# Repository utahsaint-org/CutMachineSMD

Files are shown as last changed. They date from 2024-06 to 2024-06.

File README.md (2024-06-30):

# CutMachineSMD

The Resistor and LED Cutting machine is a community project to make mass-production of small SMD components cut to specific unit sizes faster and easier to make for our highly popular MiniBadge initiatives and standards.  This machine has been used in mass-production and works great for feeding and cutting several component types.

#### Key Features
- SMD Tape Cutting
- Custom Menu-Driven Calibration Settings
- Test Cutting and Program Cutting
- Sharpie Attachment to allow color-coding of components as they are cut
- Community Contribution

# Parts List:  

For convenience I have an Amazon List for most parts: https://a.co/ecXTVj9

- 2020 Extruded Aluminium cut to
  - 2x 30cm - Top/Bottom
  - 3x 26cm - Verticals
  - 2x 20cm - Legs
  - 1x 155mm - Horizontal Crossmember
  - 1x 155mm - Roll Attachment Crossmember (Optional)
- 2020 Series Connectors and Corner Bracket Set (30 Piece)
- Bracket L-Type Internal Connectors for 2020 Series
- 4x 2020 Series Rubber Feet
- Stepper Motors
  - NEMA23 4.2Amp Motor (StepperOnline 23HS45-4204S)
  - NEMA17 1.2Amp Motor (StepperOnline 17HS19-2004S)
- Motor Drivers
  - 1x EASON Stepper Motor Driver TB6600 4A
  - 2x Stepper Motor Driver DRV8825
- Cutting Blades - 9mm Knife Replacement Blade Cartridge
- Electronics
  - Arduino Uno R3 or similar device.
  - HiLetgo CNC Drive Expansion Board (CNC Shield)
  - 2.42" 128x64 OLED LCD Display (SSD1309) i2C
- M3 Hardware
  - Assorted M2 Length Screws, Nuts, Washers
  - Assorted M3 Length Screws, Nuts, Washers
  - Assorted M5 Length Screws, Nuts, Washers
  - M3 Lever Steering Linkage
  - M3 Link Strut shaft 35mm
- 1x Miniature Linear Sliding Guideway Rail 150mm
- Power Supplies
  - 12VDC 15A Linear Power Supply
  - 12VDC to 5VDC Stepdown Regulator to power the Arduino (Optional)
- Components for PCBs ([Digikey](https://digikey.com)/[Mouser](https://mouser.com) or Similar)
  - 4x 6mm THT PushButton Switchs
  - 6x 10KΩ SMD  1206 Resistors
  - 1x 220Ω SMD  1206 Resistor
  - 1x 2.2KΩ SMD 1206 Resistor
  - 7+ Position Right-Angle PIN Headers
  - 3+ Position Straight PIN Headers
- PCBs Ordered (JLC_PCB or Similar)
  - [1x Button_Board](https://github.com/utahsaint-org/CutMachineSMD/tree/main/CuttingMachine_PCB/Buttons/Gerbers) 
  - [2x Sensor_Board](https://github.com/utahsaint-org/CutMachineSMD/tree/main/CuttingMachine_PCB/Sensor/Gerbers)
    
# Setup and Configuration

### OLED Screen Modification
The OLED screen typically comes configured for SPI interface, and we are using I2C protocol in this project.   As such, you will need to modify the OLED screen by bridging several solder pads to put the screen into I2C configuration.   You will need to disconnect the ribbon-cable and underneath you will need to bridge the solder pads labeled: R9, R10, R11, R12.  You will also need to remove the Resistor labeled R8. (Follow the published instructions for the screen to make this modification)

### Building the Framework
The Framework for the machine is fairly stratight-forward.  The 30cm struts are mounted as the top and bottom rails.  Use normal corner attachments to make the connections.  The 26cm vertical struts are attached with one in the middle and the other two are attached on the edges to make a 30cm x 30cm frame.  The center vertical is attached at 105mm spacing from center to center or 85mm Internal spacing.  You can use the Acrylic Cut Head mount as the spacing guide.   Lastly the cross-member can be attached at the approximate horizontal mid-point (125mm internal spacing).  20cm Legs are mounted horizontally outside the frame for stability.  The frame with mounted motors becomes back-heavy so I personally offset the legs to favor the back side for better support.

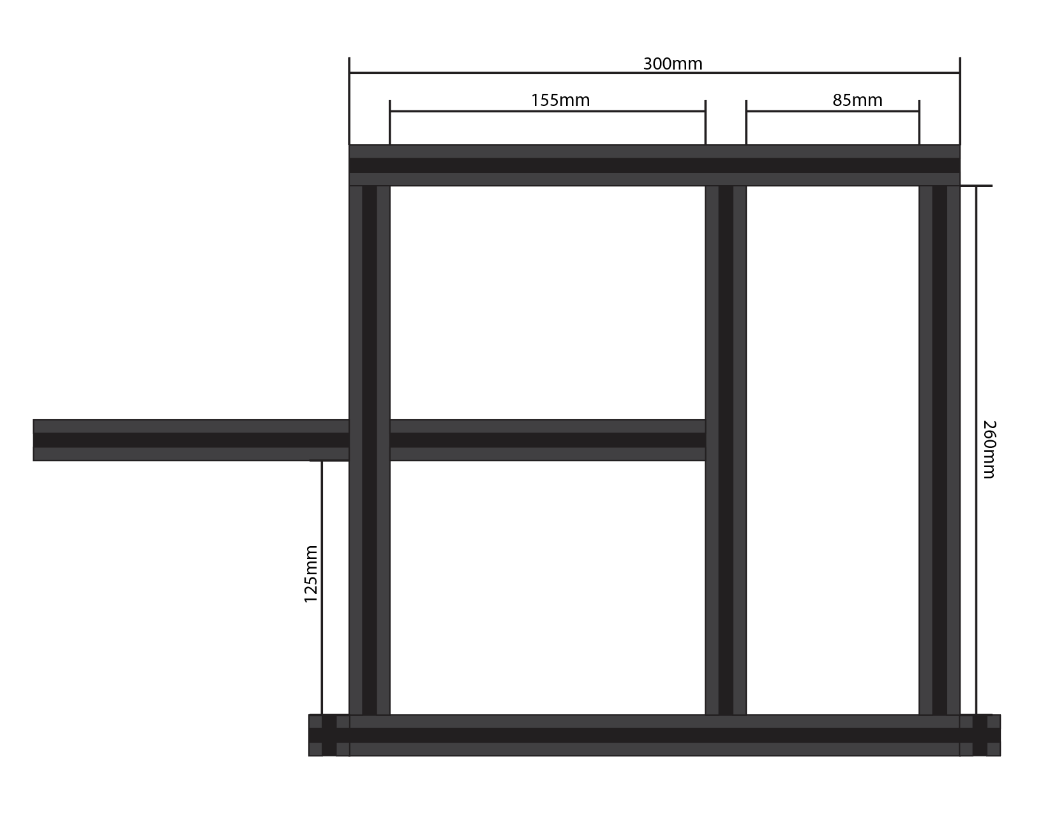
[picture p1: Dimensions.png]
Frame Dimensions


### Power Supply
Picking the right power-supply is an important aspect of any Stepper Motor configuration.   For this machine I used a 12v 15A capable power supply.   This provided all of the power I needed to run both motors and the arduino electronics.

### 3D Printing
Several of the STL designs need **supports** to be printed to ensure they are printed correctly.
NOTE: There are two Cut Heads.  One for Resistors and one for LEDs.

### Assembly
Here is what you are building:
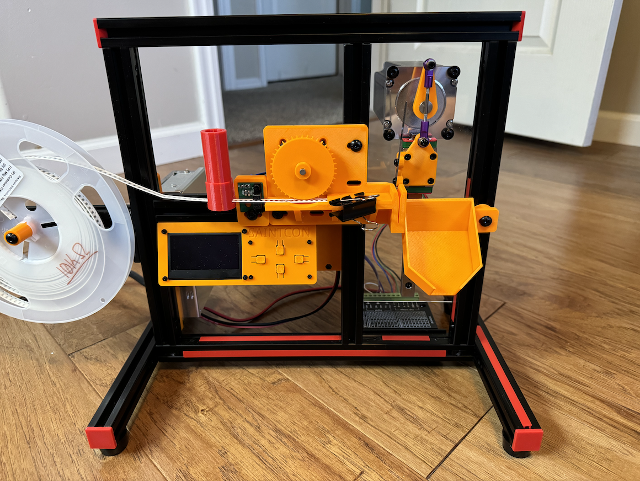
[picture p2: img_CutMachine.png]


- Build the Framework as described above.
- Attach the AcrylicCutHead on the Back Side of the machine
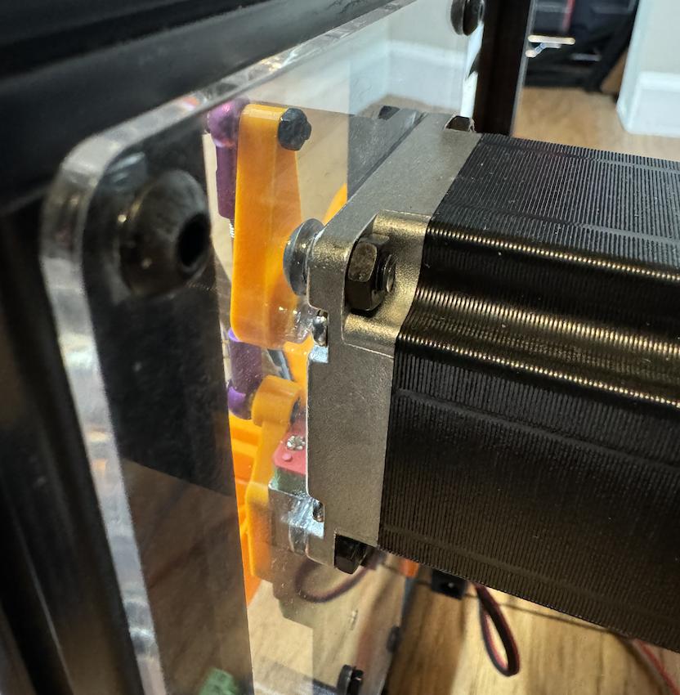
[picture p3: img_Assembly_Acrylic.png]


- Attach a RazorBlade to the Printed CutHead on the outside
  - Bottom Screw goes THRU the hole on the blade
  - Top Screw squeezes the blade to the head using a washer
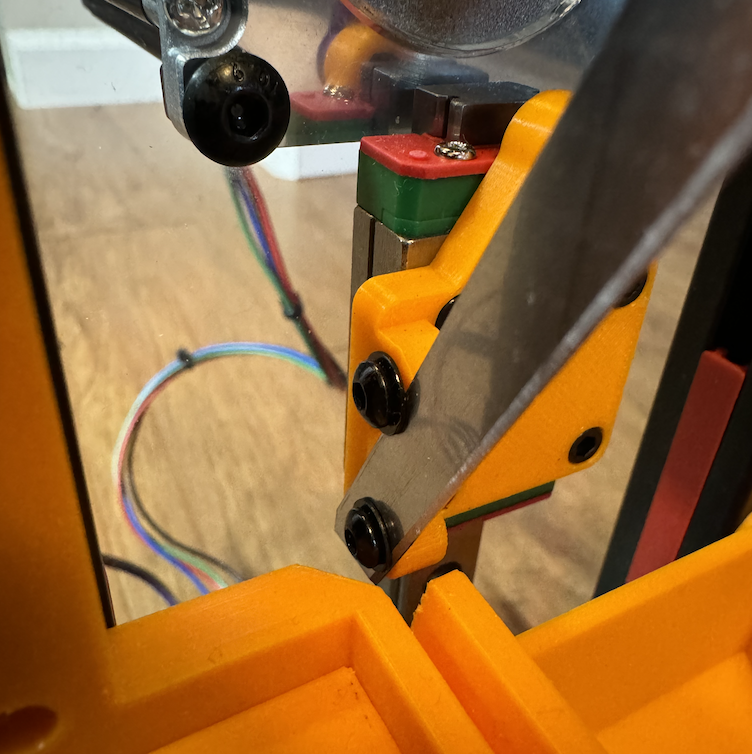
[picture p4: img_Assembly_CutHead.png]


- Attach the Razor CutHead to the Slider Rail
- Attach the FeedHead to the center rails (Horizontal and Vertical)
  - Align the razor to the slit of the Feedhead
- Attach and Connect the Display (See connections diagram)

### Firmware and Flashing
The Firmware is available in the repo.  Use the Arduino IDE application to program the Arduino board.  There are several sources of documentation or videos that can instruct you on how to install and use this program.  If you have issues, limited technical support is available on the <a href=https://discord.gg/saintcon>SAINTCON Discord Server</a> #minibadge-creators

You will need to install the following libraries:
- Adafruit GFX
- Adafruit SSD1306 Display

**Board Type should be Arduino Uno (R3)**

Open the *CuttingMachine_Firmware.ino* in the Arduino IDE program
Compile and upload the Firmware using the appropriate COM Port

### Connections
Connections for all of the components are outlined in the diagram below.

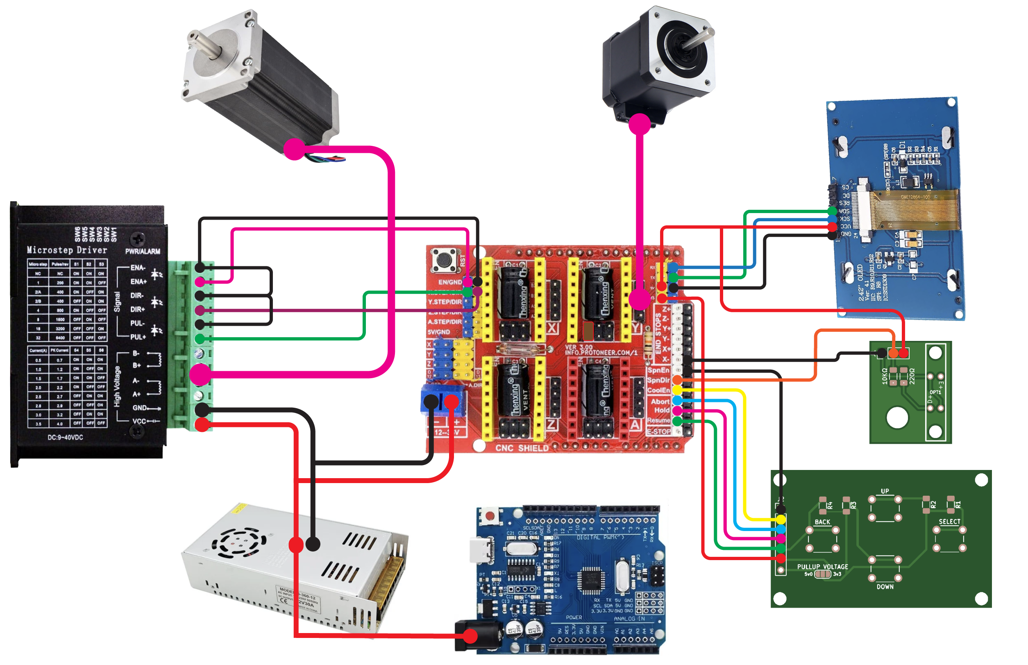
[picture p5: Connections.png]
Electrical Connections


### PCB Boards
The PCB Boards Gerbers are included in this repo.  The following instructions will help you assemble the boards and connect them properly.

#### Button_Board
- R1, R2, R3, R4 are all **10k Ohm** resistors.
- Buttons are THT 6mm Momentary Switch.
- Right-angle PIN HEADERS are suggested exiting out the back.
- Use a Solder Jumper to connect either 5v or 3v3. (Recommended you use 3v3)
- Attach the Board with M2 Screws/Bolts to the Display Controller.
- Attach the Connectors to CNC Shield as labeled in the Connections Diagram.

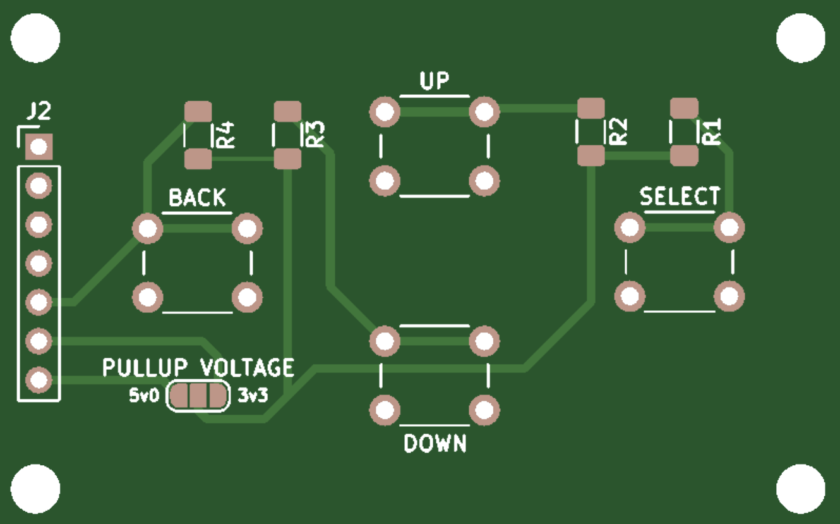
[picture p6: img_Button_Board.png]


#### Sensor_Board
- R1 is 10K Ohm
- R2 is 470 Ohm (if using it as presence sensor)
- R2 is 2.2K Ohm (If used as tape position sensor)
- PIN HEADERS are 3 Position
- Attach the Board with the M5 Screw to the FeedHead
  
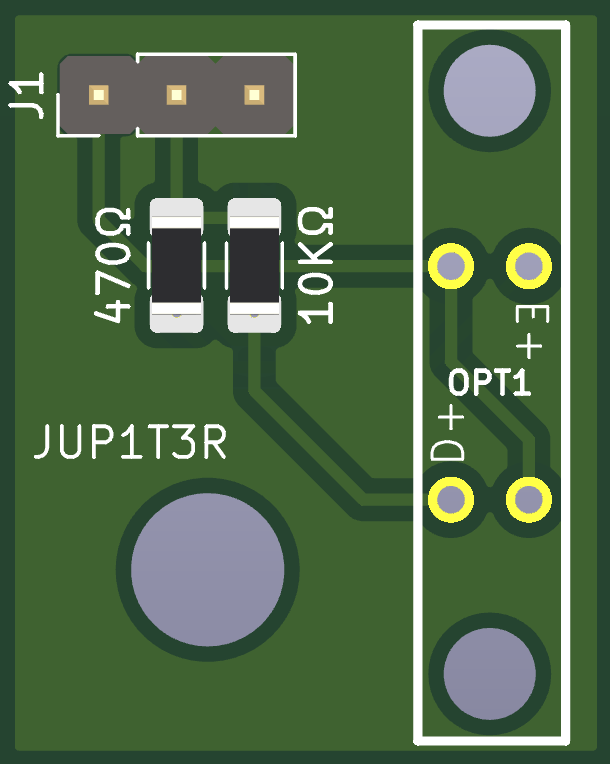
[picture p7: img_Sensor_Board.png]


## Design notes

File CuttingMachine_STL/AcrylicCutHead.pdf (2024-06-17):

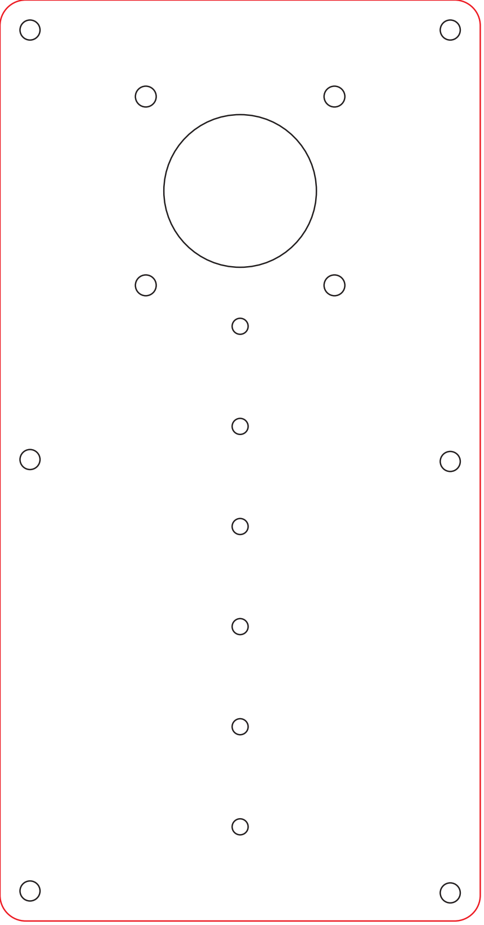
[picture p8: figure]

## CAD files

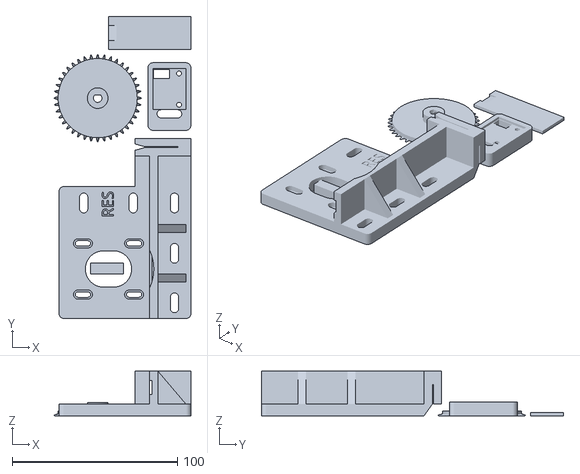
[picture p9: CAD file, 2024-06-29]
CuttingMachine_STL/RES-Cut-Head-MK11.stl
83.0 x 183.0 x 27.0

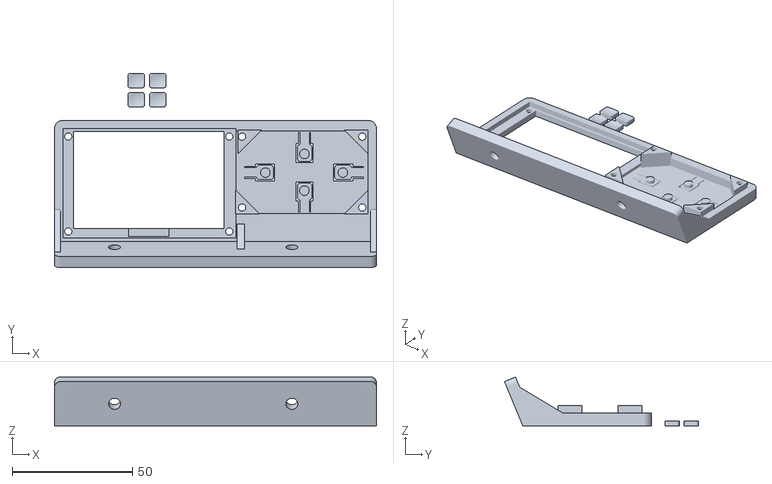
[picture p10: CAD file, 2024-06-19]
CuttingMachine_STL/Display-Face-Buttons-MK10.stl
134.0 x 80.8 x 20.4

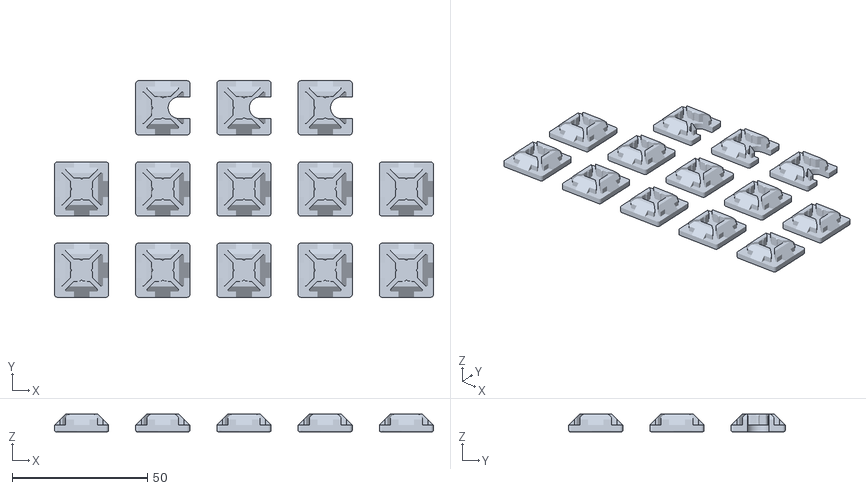
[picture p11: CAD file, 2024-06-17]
CuttingMachine_STL/EndCaps-2024-MK10.stl
140.0 x 80.0 x 6.50

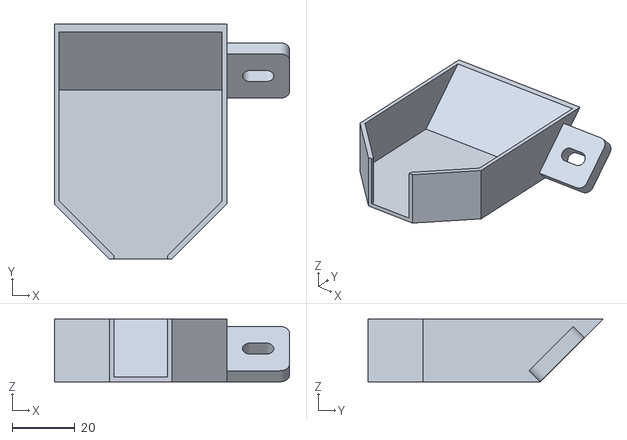
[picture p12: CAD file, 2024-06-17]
CuttingMachine_STL/Collection-Tray-2024-MK10.stl
75.0 x 75.0 x 20.0

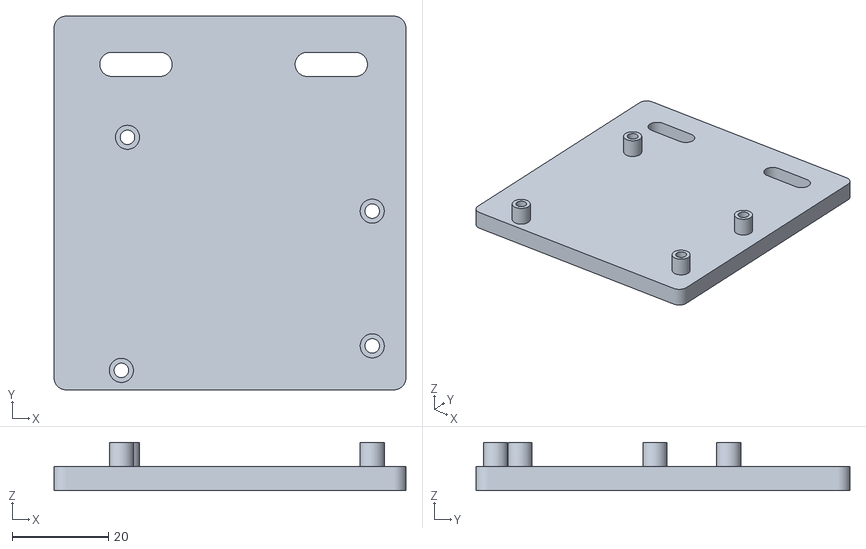
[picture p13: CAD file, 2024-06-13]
CuttingMachine_STL/Arduino-Holder-2024-MK10.stl
73.0 x 77.5 x 10.0

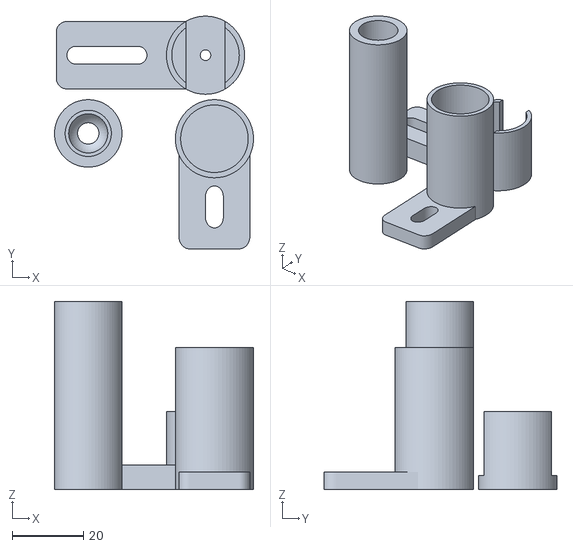
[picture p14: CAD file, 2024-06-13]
CuttingMachine_STL/Sharpie-Holder-MK11.stl
56.0 x 65.5 x 53.0

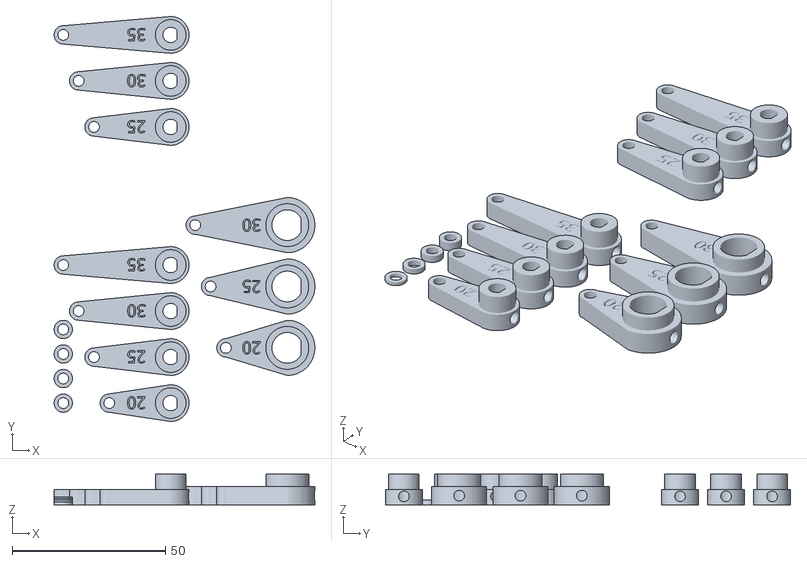
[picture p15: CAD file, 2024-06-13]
CuttingMachine_STL/Cutting-Arm-2024-MK10.stl
85.0 x 132.0 x 10.0

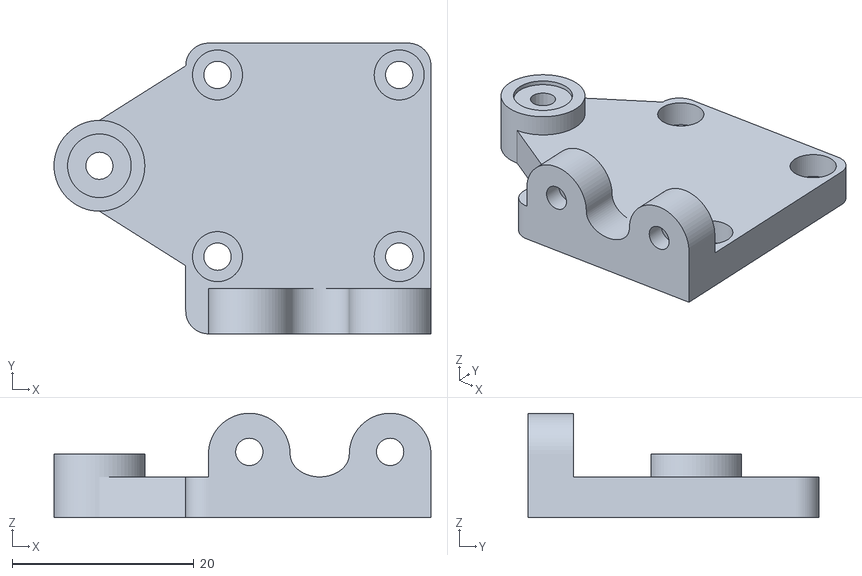
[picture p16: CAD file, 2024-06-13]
CuttingMachine_STL/Cutting-Head-2024-MK10.stl
41.5 x 32.0 x 11.5

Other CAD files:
CuttingMachine_STL/LED-Cut-Head-MK11.stl

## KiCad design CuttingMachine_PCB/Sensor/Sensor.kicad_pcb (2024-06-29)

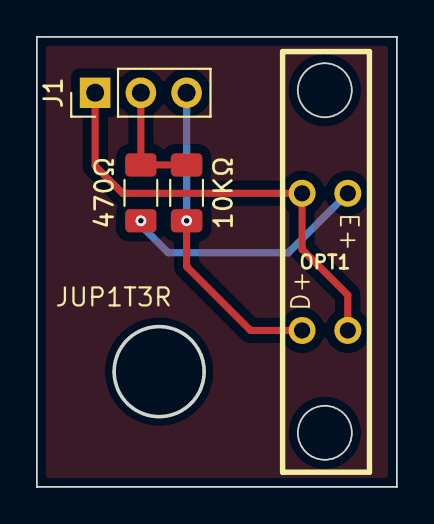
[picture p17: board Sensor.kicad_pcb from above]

Board: 2 copper layers, 20.0 x 25.0 mm, 4 parts (0 on the bottom side), 4 nets.

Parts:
10KΩ: 220; R_1206_3216Metric_Pad1.30x1.75mm_HandSolder
470Ω: 10k; R_1206_3216Metric_Pad1.30x1.75mm_HandSolder
J1: Conn_01x03_Pin; PinHeader_1x03_P2.54mm_Vertical
OPT1: MOC7811

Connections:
unnamed: J1.1, OPT1.2 (E-), OPT1.4 (D-)
unnamed: 10KΩ.1, 470Ω.1, J1.2
unnamed: 10KΩ.2, J1.3, OPT1.3 (D+)
unnamed: 470Ω.2, OPT1.1 (E+)

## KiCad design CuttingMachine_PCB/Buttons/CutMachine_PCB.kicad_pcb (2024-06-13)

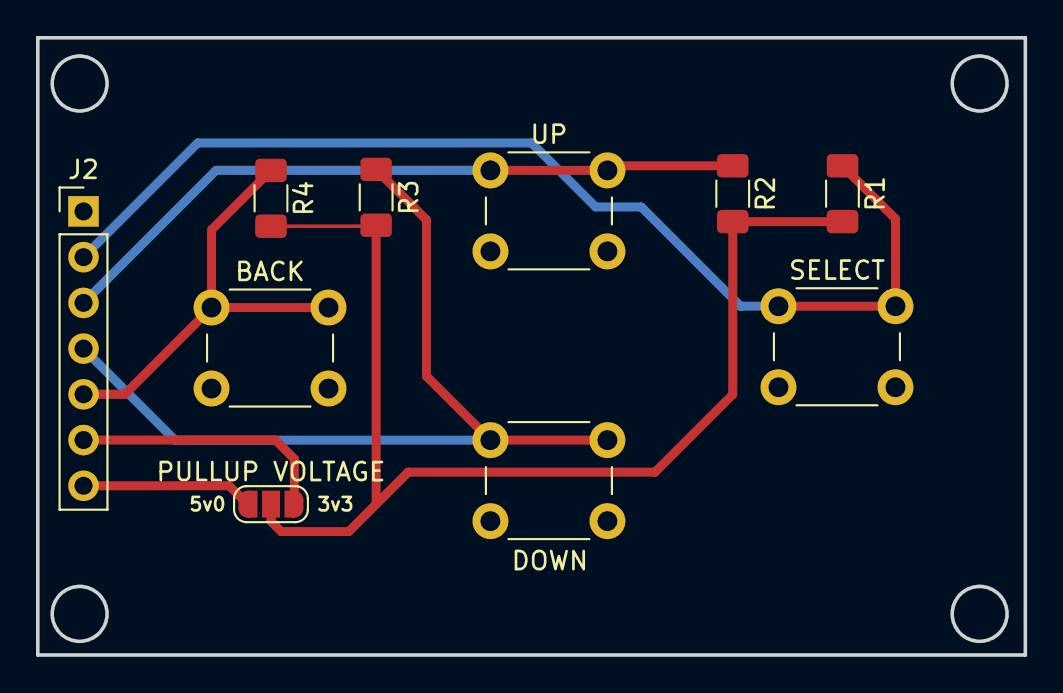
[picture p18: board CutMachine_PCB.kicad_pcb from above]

Board: 2 copper layers, 54.9 x 34.3 mm, 10 parts (0 on the bottom side), 8 nets.

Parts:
BACK: BACK; SW_PUSH_6mm_H4.3mm
J2: Conn_01x07_Pin; PinHeader_1x07_P2.54mm_Vertical
PULLUP VOLTAGE: SolderJumper_3_Open; SolderJumper-3_P1.3mm_Open_RoundedPad1.0x1.5mm_NumberLabels
R1, R2, R3, R4: PULLUP; R_1206_3216Metric_Pad1.30x1.75mm_HandSolder
SELECT: SELECT; SW_PUSH_6mm_H4.3mm
SW3: DOWN; SW_PUSH_6mm_H4.3mm
UP: UP; SW_PUSH_6mm_H4.3mm

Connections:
+3.3V: J2.6, PULLUP VOLTAGE.3 (B)
+5V: J2.7, PULLUP VOLTAGE.1 (A)
GND: BACK.2, J2.1, SELECT.2, SW3.2, UP.2
unnamed: J2.2, R1.1, SELECT.1
unnamed: J2.3, R2.1, UP.1
unnamed: J2.4, R3.1, SW3.1
unnamed: BACK.1, J2.5, R4.1
unnamed: PULLUP VOLTAGE.2 (C), R1.2, R2.2, R3.2, R4.2

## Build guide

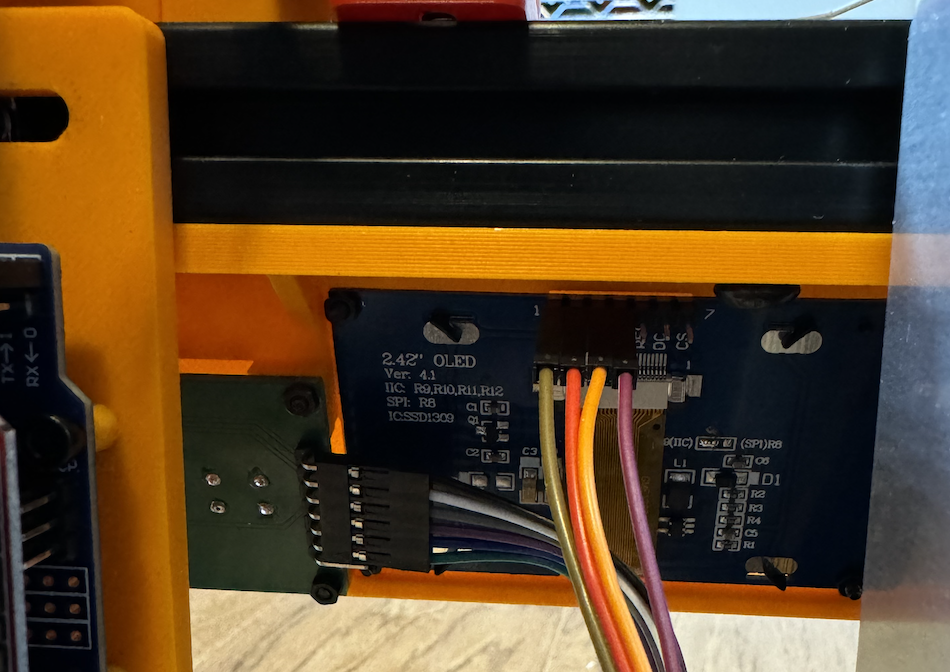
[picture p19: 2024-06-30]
img_Assembly_Display.png

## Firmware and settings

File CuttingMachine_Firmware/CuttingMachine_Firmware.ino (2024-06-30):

#include <Wire.h>

#include <Adafruit_GFX.h> // Library for GFX
#include <Adafruit_SSD1306.h> // Library for the OLED Screen
#include <avr/wdt.h> // Library for Watchdog
#include <avr/sleep.h> // Library to Sleep

#include "Assets.h" // Library of Images and Bitmaps
#include "Actions.h" // Library of most machine actions

#define version "1.0.5" // Several Updates
#define cuttype "RES" // RES or LED set for Different Types

#define SCREEN_WIDTH 128
#define SCREEN_HEIGHT 64
#define OLED_RESET - 1
Adafruit_SSD1306 display(SCREEN_WIDTH, SCREEN_HEIGHT, & Wire, OLED_RESET);

// Define buttons
#define BUTTON_UP A0
#define BUTTON_DOWN A1
#define BUTTON_BACK A2
#define BUTTON_SELECT A3
// Define Sensors
#define SENSOR_TAPE 13
#define SENSOR_UNIT 12

#define CUT_STEP 2 // Cutter Motor Stepper Pin
#define CUT_DIR 5 // Cutter Motor Direction Pin
#define FEED_STEP 3 // Feeder Motor Stepper Pin
#define FEED_DIR 6 // Feeder Motor Direction Pin
#define ENABLE 8 // Motor Enable Pin

int menuIndex = 0;
int submenuIndex = 0;
bool inSubMenu = false;
unsigned long lastActivityTime = 0;
const unsigned long inactivityTimeout = 600000;  // 10 Minutes in milliseconds

// Default Variable Settings
int setSize = 1; // Size of the units |*|*|*|*|*|
int setUnits = 1; // How many pieces get cut by default
int setInterval = 4; // Tape Interval in millimeters

// Debounce settings
const unsigned long debounceDelay = 300; // milliseconds
unsigned long lastDebounceTime = 10;

void setup() {
  // Setup Buttons used for Navigation (Up, Down, Back, Select)
  pinMode(BUTTON_UP, INPUT_PULLUP);
  pinMode(BUTTON_DOWN, INPUT_PULLUP);
  pinMode(BUTTON_BACK, INPUT_PULLUP);
  pinMode(BUTTON_SELECT, INPUT_PULLUP);
  // Setup PIN for Tape Presence Sensor
  pinMode(SENSOR_TAPE, INPUT);
  // Setup PINs for Motor Controls for Feed and Cut
  pinMode(CUT_STEP, OUTPUT);
  pinMode(CUT_DIR, OUTPUT);
  pinMode(FEED_STEP, OUTPUT);
  pinMode(FEED_DIR, OUTPUT);
  // Setup PIN for enableing Motors
  pinMode(ENABLE, OUTPUT);
  // Disable Motors until we enter Main Menu HIGH == DISABLED
  digitalWrite(ENABLE, HIGH);

  // Initialize the OLED display
  display.begin(SSD1306_SWITCHCAPVCC, 0x3C);
  display.clearDisplay();
  // Display Firmware and Logo
  FirmwareDisplay();      //Display Firmware Version
  LogoDisplay();          //Display Logo Bootscreen
}

  // Define Frame Control Variable for graphics
  int frame=0;

void loop() {
  // Watch for SELECT Button to enter the Menu
  if (readButton(BUTTON_SELECT) == true) {
    lastActivityTime = millis();
    navigateMenu();
  }
  // Disable Motors if the UP Button was pressed in Idle Screen
  if (readButton(BUTTON_UP) == true) { 
    digitalWrite(ENABLE, HIGH); 
    lastActivityTime = millis();
  }
  // Watch for inactivity and enter sleep mode
  if (millis() - lastActivityTime > inactivityTimeout) {
    enterSleepMode();
  }
  // Display the Idle Screen Details
  display.clearDisplay();
  display.drawBitmap(78, 0, frames[frame], FRAME_WIDTH, FRAME_HEIGHT, 1);
  display.setCursor(0, 0);
  display.setTextSize(2);
  display.println(F("IDLE"));
  display.setTextSize(1);
  display.print(F("Size: "));
  display.println(setSize);
  display.print(F("Units: "));
  display.println(setUnits);
  // Show the state of the Tape Sensor
  if (digitalRead(SENSOR_TAPE) == LOW) {
    display.println(F("Sensor: LOW"));
  } else {
    display.println(F("Sensor: HIGH"));
  }
  // Show the state of Unit Sensor
  if (digitalRead(SENSOR_UNIT) == LOW) {
    display.println(F("Sensor: LOW"));
  } else {
    display.println(F("Sensor: HIGH"));
  }
  // Show the state of the Motors
  if (digitalRead(ENABLE) == LOW) {
    display.println(F("Motors: ENABLED"));
  } else {
    display.println(F("Motors: DISABLED"));
  }
  display.println(F("Press SELECT to Start"));
  display.display();
  frame = (frame + 1) % FRAME_COUNT;
  delay(FRAME_DELAY);
}


// Process to handle Button Press Bounces (Smooth UI Handling)
bool readButton(int buttonPin) {
  if (digitalRead(buttonPin) == LOW) {
    // Do no detect the press unless its longer than debounceDelay value
    if (millis() - lastDebounceTime > debounceDelay) {
      lastDebounceTime = millis();
      return true;
    }
  }
  return false;
}

// Firmware Screen display
void FirmwareDisplay() { display.clearDisplay(); display.setTextColor(WHITE); display.setTextSize(1); display.print(F("Firmware: ")); display.println(F(version)); display.display(); delay(1000); }
// Logo Boot display
void LogoDisplay() { display.clearDisplay(); display.drawBitmap(0, 0, SCLOGO, 128, 64, SSD1306_WHITE); display.display(); delay(1500);}

// Main Menu Navigation Routine
void navigateMenu() {
  // Enable Motors if the Menu is entered (sticky)
  digitalWrite(ENABLE, LOW);
  while (true) {
    displayMenu();
    if (readButton(BUTTON_SELECT) == true) {
      if (inSubMenu) {
        executeSubmenuOption();
      } else {
        enterSubMenu();
      }
    } else if (readButton(BUTTON_BACK) == true) {
      if (inSubMenu) {
        inSubMenu = false;
        submenuIndex = 0;
      } else {
        //displayIdleScreen();
        return;
      }
    } else if (readButton(BUTTON_UP) == true) {
      if (inSubMenu) {
        submenuIndex = (submenuIndex > 0) ? submenuIndex - 1 : getMaxSubMenuIndex();
      } else {
        menuIndex = (menuIndex > 0) ? menuIndex - 1 : 4; // Adjust this for Menu Number
      }
    } else if (readButton(BUTTON_DOWN) == true) {
      if (inSubMenu) {
        submenuIndex = (submenuIndex < getMaxSubMenuIndex()) ? submenuIndex + 1 : 0;
      } else {
        menuIndex = (menuIndex < 4) ? menuIndex + 1 : 0; // Adjust this for Menu Number
      }
    }
  }
}

void displayMenu() {
  display.clearDisplay();
  display.setTextColor(SSD1306_WHITE);
  display.setTextSize(1);
  display.setCursor(0, 0);
  if (!inSubMenu) {
    display.setTextSize(2);
    display.println(F("MAIN MENU"));
    display.setTextSize(1);
    if (menuIndex == 0) display.println(F("> CUT!"));
    else display.println(F("  Cut!"));
    if (menuIndex == 1) display.println(F("> SETTINGS"));
    else display.println(F("  Settings"));
    if (menuIndex == 2) display.println(F("> CALIBRATE"));
    else display.println(F("  Calibrate"));
    if (menuIndex == 3) display.println(F("> LOAD TAPE"));
    else display.println(F("  Load Tape"));
    if (menuIndex == 4) display.println(F("> RESET"));
    else display.println(F("  Reset"));
  } else {
    if (menuIndex == 0) {
      display.setTextSize(2);
      display.println(F("START CUT!"));
      display.setTextSize(1);
      if (submenuIndex == 0) {
        display.setTextSize(3);
        display.println(F("> GO!"));
      } else {
        display.setTextSize(3);
        display.println(F("  Go"));
      }
      if (submenuIndex == 1) {
        display.setTextSize(1);
        display.println(F("> TEST CUT"));
      } else {
        display.setTextSize(1);
        display.println(F("  Test Cut"));
      }
    }
    if (menuIndex == 1) {
      display.setTextSize(2);
      display.println(F("SETTINGS"));
      display.setTextSize(1);
      if (submenuIndex == 0) { 
        display.print(F("> Set Size: "));
        display.println(setSize);
      } else { 
        display.print(F("  Set Size: "));
        display.println(setSize);
      }
      if (submenuIndex == 1) {
        display.print(F("> Set Units: "));
        display.println(setUnits);
      } else {
        display.print(F("  Set Units: "));
        display.println(setUnits);
      }
    }
    if (menuIndex == 2) {
      display.setTextSize(2);
      display.println(F("CALIBRATE"));
      display.setTextSize(1);
      if (submenuIndex == 0) display.println(F("> ADJUST FWD"));
      else display.println(F("  Adjust Fwd"));
      if (submenuIndex == 1) display.println(F("> ADJUST REV"));
      else display.println(F("  Adjust Rev"));
    }
    if (menuIndex ==3) {
      display.setTextSize(2);
      display.println(F("LOAD TAPE"));
      display.setTextSize(1);
      if (submenuIndex == 0) display.println(F("> LOAD TAPE"));
      else display.println(F("  Load Tape"));
      if (submenuIndex == 1) display.println(F("> UNLOAD TAPE"));
      else display.println(F("  Unload Tape"));
    }
      if (menuIndex ==4) {
      display.setTextSize(2);
      display.println("RESET?");
      display.setTextSize(1);
      if (submenuIndex == 0) display.println("> NO");
      else display.println("  No");
      if (submenuIndex == 1) display.println("> YES");
      else display.println("  Yes");
    }
  }
  display.display();
}

void enterSubMenu() {
  inSubMenu = true;
  submenuIndex = 0;
}

int getMaxSubMenuIndex() {
  switch (menuIndex) {
  case 0:
    return 1; // CUT! menu has 2 options: Go and Test Cut
  case 1:
    return 1; // Settings menu has 2 options: Set Size and Set Units
  case 2:
    return 1; // Calibrate menu has 2 options: Adjust FWD and Adjust REV
  case 3:
    return 1; // LoadTape Menu has 2 options
  case 4:
    return 1; // Reset menu has 2 options
  default:
    return 0;
  }
}

void executeSubmenuOption() {
  switch (menuIndex) {
  case 0: // CUT!
    if (submenuIndex == 0) runCutProgram();
    else if (submenuIndex == 1) runCutTest();
    break;
  case 1: // Settings
    if (submenuIndex == 0) changeSize();
    else if (submenuIndex == 1) changeUnits();
    break;
  case 2: // Calibrate
    if (submenuIndex == 0) runAdjustFWD();
    else if (submenuIndex == 1) runAdjustREV();
    break;
  case 3: // LoadTape Menu
    if (submenuIndex == 0) loadTape();
    else if (submenuIndex == 1) unloadTape();
    break;
  case 4: // Reset Menu
    if (submenuIndex == 0) resetNo();
    else if (submenuIndex == 1) resetYes();
    break;
  }
}

/// Sleep Mode Process
void enterSleepMode() {
  digitalWrite(ENABLE, HIGH);  // Disable Motors so they last longer
  lastActivityTime = millis();
  inSubMenu=false;
}

void resetNo()  { inSubMenu = false; }
void resetYes() {
  display.clearDisplay(); display.setCursor(0, 0); display.setTextSize(2); display.println(F("RESETTING!")); display.display();
  delay(2000);
  // Reboot Device
  wdt_enable(WDTO_15MS);
  while(1);
}

// Main Cutting Program
void runCutProgram() {
  display.clearDisplay();
  // Main process for Cutting
  for (int rp = 0; rp < setUnits; rp++) {
    // Display Cut Status (Units Cut)
    display.setCursor(0, 0); display.setTextSize(2); display.println("CUTTING"); display.setTextSize(3); display.setCursor(0, 24); display.print(" = "); display.println(rp + 1); display.display();
    // Sensor Check for Tape Existence (Stop and Display Error)
    if (digitalRead(SENSOR_TAPE) == LOW) {
      // Display Error Message
      display.clearDisplay(); display.setCursor(4, 7); display.setTextSize(2); display.println("!STOPPING!"); display.setTextSize(1); display.println("\n    Load or Check\n   component tape."); display.display();
      delay(500);
      // Blink the Display
      for (int i = 0; i < 20; i++) {
        if (i % 2 == 0) {
          display.invertDisplay(true);
        } else {
          display.invertDisplay(false);
        }
        display.display();
        delay(500);
      }
      // Stop and Return if the Sensor is tripped
      return;
    }
    FEED(setSize);  // Feed the Tape based on the Size Selected
    CUT();  // Cut the tape after the feed is complete
    lastActivityTime = millis();  // Keep from entering sleepMode while cutting
  }
  // Clear the cut head
  ClearFeeder(); // Clears the Feed Head
  delay(200);
  inSubMenu = false;
}

// This will cut one component and make one unit
// This is just for testing
void runCutTest() {
  FEED(1);
  CUT();
  ClearFeeder();
  delay(500);
  inSubMenu = false;
}

void ClearFeeder() {
  int ClearCount = 10;
  digitalWrite(FEED_DIR, LOW); // Set Forward
  for (int y = 0; y < ClearCount; y++) {
    digitalWrite(FEED_STEP, HIGH);
    delayMicroseconds(1700); // Fast Rotation
    digitalWrite(FEED_STEP, LOW);
    delayMicroseconds(1700); // Fast Rotation
  }
  digitalWrite(FEED_DIR, HIGH); // Set Reverse
  for (int y = 0; y < ClearCount; y++) {
    digitalWrite(FEED_STEP, HIGH);
    delayMicroseconds(1700); // Fast Rotation
    digitalWrite(FEED_STEP, LOW);
    delayMicroseconds(1700); // Fast Rotation
  }
  digitalWrite(FEED_DIR, LOW);
}

// Main CUT Process (One Full Rotation)
void CUT() {
  int cutsteps = 800;
  for (int x = 0; x < cutsteps; x++) {
    digitalWrite(CUT_STEP, HIGH);
    delayMicroseconds(90); // Fast Rotation
    digitalWrite(CUT_STEP, LOW);
    delayMicroseconds(90); // Fast Rotation
    display.clearDisplay();
  }
  delay(100);
}

// Main FEED Process
void FEED(int feedcount) {
  int feedsteps = feedcount * 10;
  digitalWrite(FEED_DIR, LOW); // Set Feed Forward for Feed
  for (int y = 0; y < feedsteps; y++) {
    digitalWrite(FEED_STEP, HIGH);
    delayMicroseconds(700); // Fast Rotation
    digitalWrite(FEED_STEP, LOW);
    delayMicroseconds(700); // Fast Rotation
  }
  delay(100);
}

// Future Tape Loading
void loadTape() {
  display.clearDisplay();
  display.setCursor(0, 0);
  display.println(F("LOAD Function not\nimplemented"));
  display.display();
  delay(2000);
}
// Future Tape Unloading
void unloadTape() {
  display.clearDisplay();
  display.setCursor(0, 0);
  display.println(F("UNLOAD Function not\nimplemented"));
  display.display();
  delay(2000);
}

void changeSize() {
  while (true) {
    if (readButton(BUTTON_UP) == true && setSize < 1000) setSize++;
    else if (readButton(BUTTON_DOWN) == true && setSize > 1) setSize--;
    //delay(150);
    if (readButton(BUTTON_SELECT) == true) break;
    display.clearDisplay();
    display.setCursor(0, 0);
    display.setTextSize(2);
    display.print("SET SIZE\n");
    display.setCursor(4, 17);
    display.setTextSize(3);
    display.println(setSize);
    // Display the size of the unit
    if (setSize >= 1) { display.drawBitmap(0, 51, RES, 7, 14, SSD1306_WHITE); }
    if (setSize >= 2) { display.drawBitmap(7, 51, RES, 7, 14, SSD1306_WHITE); }
    if (setSize >= 3) { display.drawBitmap(14, 51, RES, 7, 14, SSD1306_WHITE); }
    if (setSize >= 4) { display.drawBitmap(21, 51, RES, 7, 14, SSD1306_WHITE); }
    if (setSize >= 5) { display.drawBitmap(28, 51, RES, 7, 14, SSD1306_WHITE); }
    if (setSize >= 6) { display.drawBitmap(35, 51, RES, 7, 14, SSD1306_WHITE); }
    if (setSize >= 7) { display.drawBitmap(42, 51, RES, 7, 14, SSD1306_WHITE); }
    if (setSize >= 8) { display.drawBitmap(49, 51, RES, 7, 14, SSD1306_WHITE); }
    if (setSize >= 9) { display.drawBitmap(56, 51, RES, 7, 14, SSD1306_WHITE); }
    if (setSize >= 10) { display.drawBitmap(63, 51, RES, 7, 14, SSD1306_WHITE); }
    if (setSize >= 11) { display.drawBitmap(70, 51, RES, 7, 14, SSD1306_WHITE); }
    if (setSize >= 12) { display.drawBitmap(77, 51, RES, 7, 14, SSD1306_WHITE); }
    if (setSize >= 13) { display.drawBitmap(84, 51, RES, 7, 14, SSD1306_WHITE); }
    if (setSize >= 14) { display.drawBitmap(91, 51, RES, 7, 14, SSD1306_WHITE); }
    if (setSize >= 15) { display.drawBitmap(98, 51, RES, 7, 14, SSD1306_WHITE); }
    if (setSize >= 16) { display.drawBitmap(105, 51, RES, 7, 14, SSD1306_WHITE); }
    if (setSize >= 17) { display.drawBitmap(112, 51, RES, 7, 14, SSD1306_WHITE); }
    if (setSize >= 18) { display.drawBitmap(119, 51, RES, 7, 14, SSD1306_WHITE); }
    display.display();
  }
}

void changeUnits() {
  while (true) {
    if (readButton(BUTTON_UP) == true && setUnits < 1000) setUnits++;
    else if (readButton(BUTTON_DOWN) == true && setUnits > 1) setUnits--;
    //delay(100);
    if (readButton(BUTTON_SELECT) == true) break;
    display.clearDisplay();
    display.setCursor(0, 0);
    display.setTextSize(2);
    display.print("SET UNITS\n");
    display.setCursor(4, 17);
    display.setTextSize(3);
    display.println(setUnits);
    display.display();
  }
}

void runAdjustFWD() {
  display.clearDisplay();
  display.setCursor(0, 0);
  display.setTextSize(2);
  display.println("ADJUSTING");
  display.setTextSize(3);
  display.println(">>> FWD");
  display.display();
  digitalWrite(FEED_DIR, LOW);
  digitalWrite(FEED_STEP, HIGH);
  delayMicroseconds(1000);
  digitalWrite(FEED_STEP, LOW);
  delay(150);
  displayMenu();
}

void runAdjustREV() {
  display.clearDisplay();
  display.setCursor(0, 0);
  display.setTextSize(2);
  display.println("ADJUSTING");
  display.setTextSize(3);
  display.println("<<< REV");
  display.display();
  digitalWrite(FEED_DIR, HIGH);
  digitalWrite(FEED_STEP, HIGH);
  delayMicroseconds(1000);
  digitalWrite(FEED_STEP, LOW);
  delay(150);
  displayMenu();
}

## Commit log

2024-06-13 SLT and KiCAD Files
    [Arduino-Holder-2024-MK10.stl, Collection-Tray-2024-MK10.stl, CutHead-Sprocket-2024-MK10.stl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]
2024-06-13 LaserCut Template
    LaserCut for Acrylic object. This can also be 3D printed if needed.
2024-06-13 Framework Assembly
2024-06-17 Updates for prints
    [Collection-Tray-2024-MK10.stl, Display-Face-Buttons-MK10.stl, EndCaps-2024-MK10.stl]
2024-06-21 Updated Assets, Added Detection Sensor
2024-06-22 Fixed error where display in settings menu was not working
    [CuttingMachine_Firmware.ino]
2024-06-28 Fixed Error in Sensor board
    [Sensor-B_Cu.gbr, Sensor-B_Mask.gbr, Sensor-B_Paste.gbr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]
2024-06-29 Revert "Update CuttingMachine_Firmware.ino"
    This reverts commit 331047baca9097e741e2c189d087a95fc5961f25.
    [Sensor.kicad_pcb]
2024-06-29 Updated STL Files (Added LED Head)
    [CutHead-Sprocket-2024-MK10.stl, LED-Cut-Head-MK11.stl, RES-Cut-Head-MK11.stl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]
2024-06-29 Fixed issue that make the settings menu not display properly.
    [CuttingMachine_Firmware.ino]
2024-06-30 Added Reset and Sleep functions
    [CuttingMachine_Firmware.ino]
